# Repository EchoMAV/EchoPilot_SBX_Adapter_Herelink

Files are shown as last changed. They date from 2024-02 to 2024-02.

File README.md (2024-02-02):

Created using KiCad 7.0.10

This is an open-source radio adapter designed for the EchoPilot SBX series of boards. It is meant for a Herelink v1.1+ air unit, but can also be used for serial telemetry and IP radios such as the RFD900 or Doodle Labs.

The board provides regulated 7.5VDC @ 2A

6 Layer PCB, 4/4 mil spacing, min hole size is 0.2mm Note impedance controlled traces for MIPI, USB and Ethernet. Trace width and spacing may need to be adjusted depending on the stackup and materials used in production.

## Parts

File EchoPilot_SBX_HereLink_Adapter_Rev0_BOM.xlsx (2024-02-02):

EchoPilot SBX HereLink Radio Adapter Rev 0
Item | Qty | Reference(s) | Value | LibPart | Footprint | Part Num
1 | 1 | C1 | 4.7nF | Device:C | Capacitor_SMD:C_0201_0603Metric | GRM033R61E472KA12D
2 | 1 | C2 | 47uF | Device:C | Capacitor_SMD:C_1206_3216Metric | C3216X5R1E476M160AC
3 | 1 | C3 | 0.1uF 100V | Device:C | Capacitor_SMD:C_0603_1608Metric | CL10B104KC8NNNC
4 | 1 | C4 | 10uF 63V | Device:C | Capacitor_SMD:C_1210_3225Metric | CL32B106KMVNNWE
5 | 1 | D1 | D_Zener | Device:D_Zener | Diode_SMD:D_SMA | SK220A
6 | 1 | D2 | LED_G | Device:LED | LED_SMD:LED_0603_1608Metric | 150060VS75000
7 | 1 | IC1 | LMR14020SQDPRRQ1 | LMR14020SQDPRRQ1:LMR14020SQDPRRQ1 | SON80P400X400X80-11N | LMR14020SQDPRRQ1
8 | 1 | J1 | DF40C-30DP-0.4V(51) | Connector_Generic:Conn_02x15_Top_Bottom | UVDL.Pretty:HRS_DF40C-30DP-0.4V_51_ | DF40C-30DP-0.4V(51)
9 | 1 | J2 | Conn_01x05 | Connector_Generic:Conn_01x05 | Connector_JST:JST_GH_SM05B-GHS-TB_1x05-1MP_P1.25mm_Horizontal | SM05B-GHS-TBT
10 | 1 | J3 | Conn_01x02 | Connector_Generic:Conn_01x02 | Connector_JST:JST_GH_SM02B-GHS-TB_1x02-1MP_P1.25mm_Horizontal | SM02B-GHS-TBT
11 | 1 | J4 | Conn_01x04 | Connector_Generic:Conn_01x04 | Connector_JST:JST_GH_SM04B-GHS-TB_1x04-1MP_P1.25mm_Horizontal | SM04B-GHS-TBT
12 | 1 | J5 | Conn_01x03 | Connector_Generic:Conn_01x03 | Connector_JST:JST_GH_SM03B-GHS-TB_1x03-1MP_P1.25mm_Horizontal | SM03B-GHS-TBT
13 | 1 | L1 | 4.7uF | Device:L | UVDL.Pretty:IND_336047_WRE | 74438336047
14 | 1 | R1 | 23.2K | Device:R | Resistor_SMD:R_0201_0603Metric | ERJ-1GNF2322C
15 | 1 | R2 | 90.9K | Device:R | Resistor_SMD:R_0201_0603Metric | ERJ-1GNF9092C
16 | 1 | R3 | 10K | Device:R | Resistor_SMD:R_0201_0603Metric | ERJ-1GNF1002C
17 | 1 | R4 | 1.0K | Device:R | Resistor_SMD:R_0201_0603Metric | ERJ-1GEF1001C

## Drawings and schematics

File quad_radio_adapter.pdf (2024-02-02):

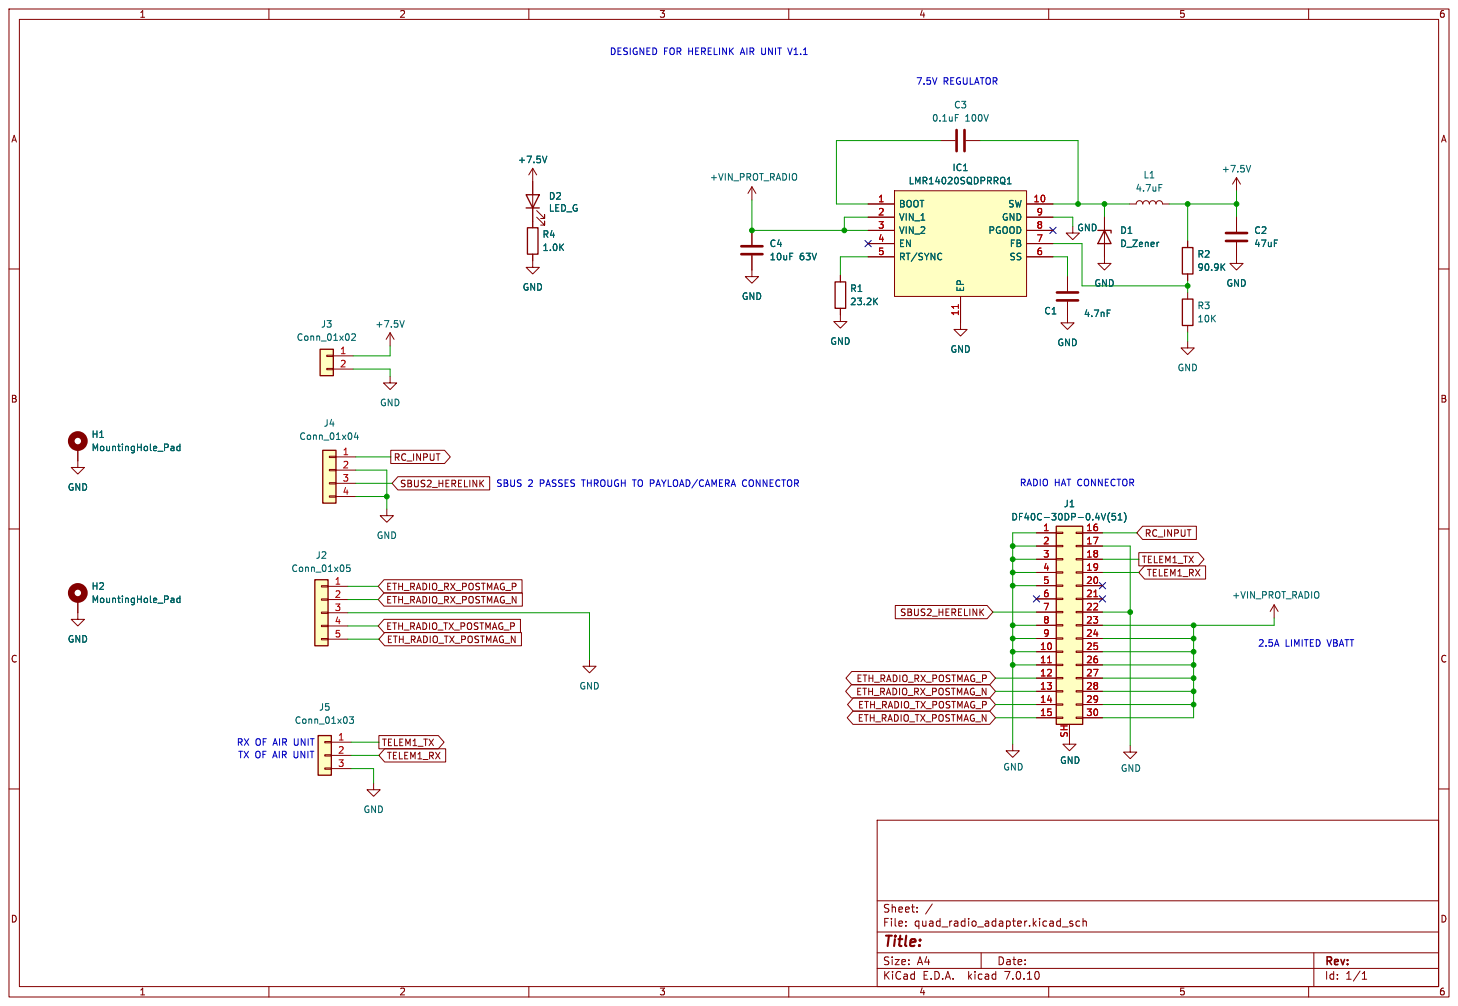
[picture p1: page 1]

TX OF AIR UNIT RX OF AIR UNIT

Id: 1/1 Title: File: quad_radio_adapter.kicad_sch Sheet: /

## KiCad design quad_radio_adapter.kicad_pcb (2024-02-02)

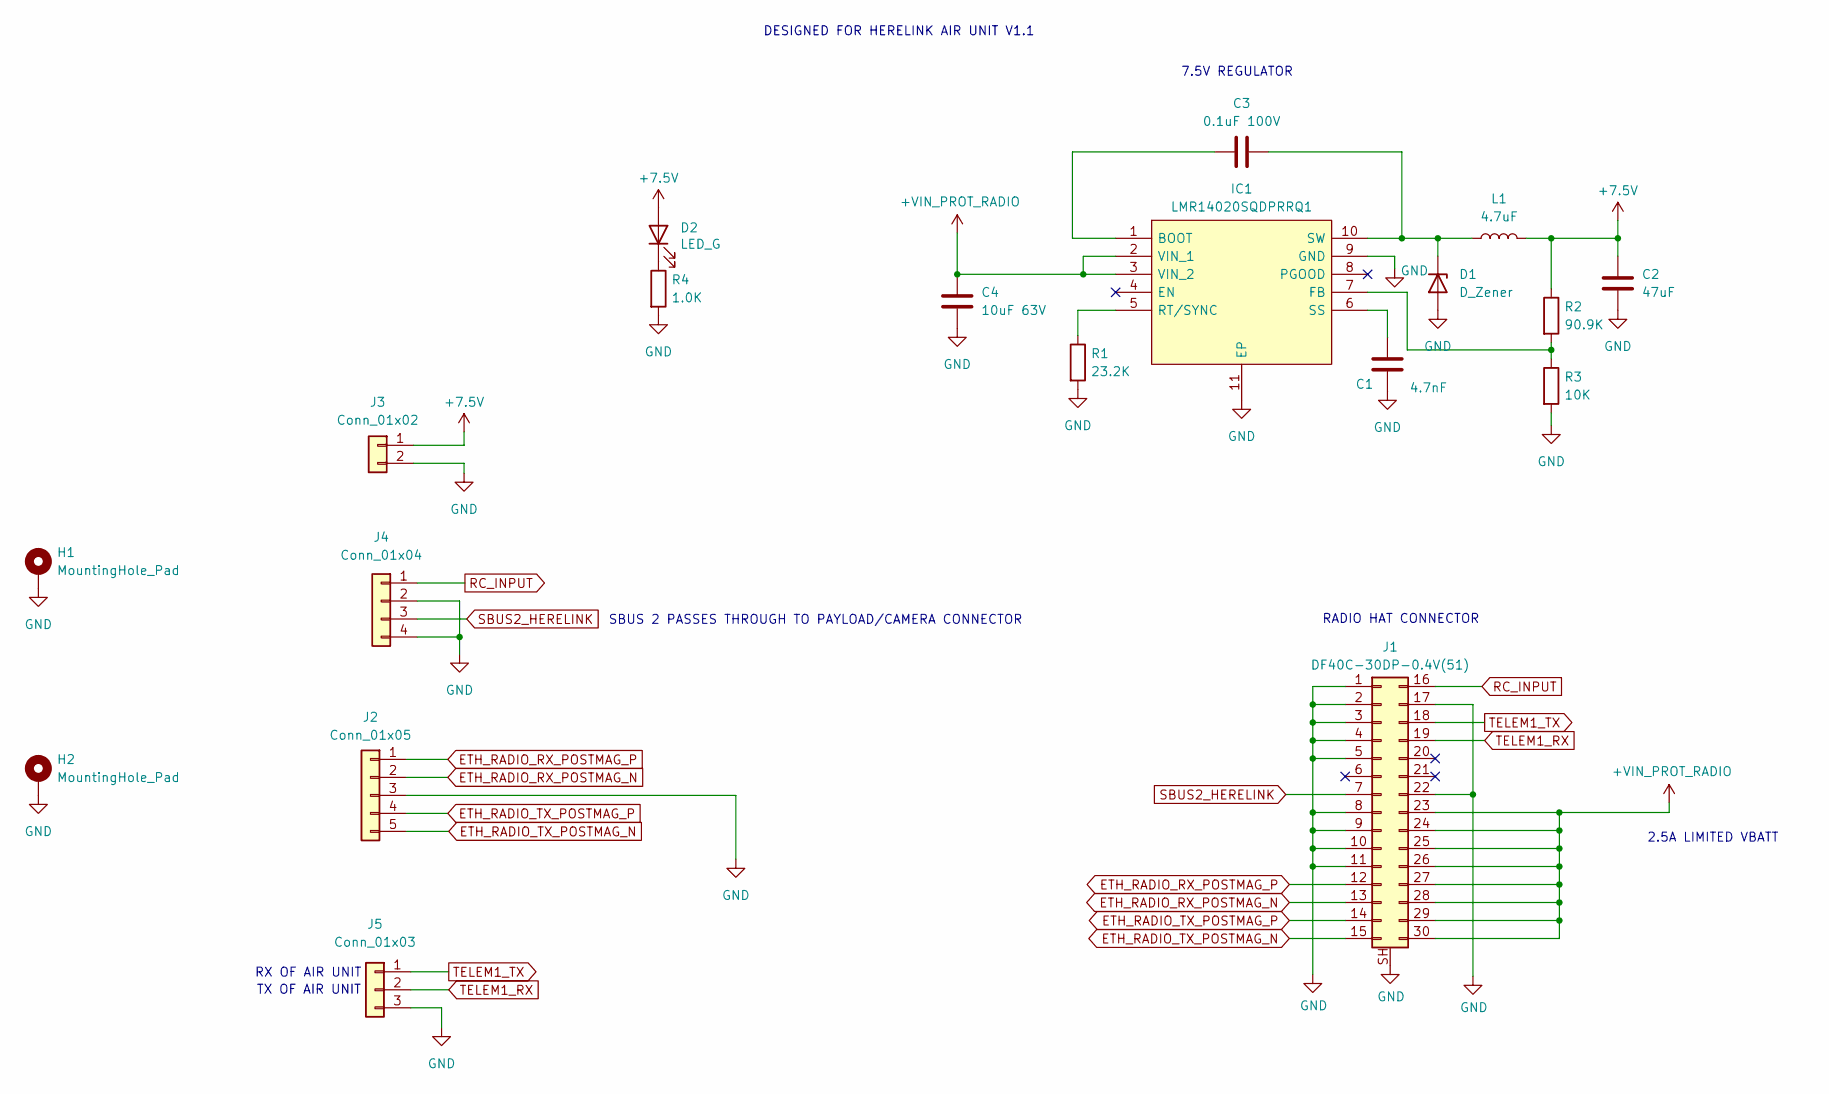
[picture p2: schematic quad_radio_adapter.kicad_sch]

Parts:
C1: 4.7nF; C_0201_0603Metric; Part Num GRM033R61E472KA12D
C2: 47uF; C_1206_3216Metric; Part Num C3216X5R1E476M160AC
C3: 0.1uF 100V; C_0603_1608Metric; Part Num CL10B104KC8NNNC
C4: 10uF 63V; C_1210_3225Metric; Part Num CL32B106KMVNNWE
D1: D_Zener; D_SMA; Part Num SK220A
D2: LED_G; LED_0603_1608Metric; Part Num 150060VS75000
H1, H2: MountingHole_Pad; MountingHole_2.2mm_M2_Pad
IC1: LMR14020SQDPRRQ1; SON80P400X400X80-11N; Manufacturer_Part_Number LMR14020SQDPRRQ1; Mouser Part Number 595-LMR14020SQDPRRQ1
J1: DF40C-30DP-0.4V(51); HRS_DF40C-30DP-0.4V_51_; Part Num DF40C-30DP-0.4V(51)
J2: Conn_01x05; JST_GH_SM05B-GHS-TB_1x05-1MP_P1.25mm_Horizontal; Part Num SM05B-GHS-TBT
J3: Conn_01x02; JST_GH_SM02B-GHS-TB_1x02-1MP_P1.25mm_Horizontal; Part Num SM02B-GHS-TBT
J4: Conn_01x04; JST_GH_SM04B-GHS-TB_1x04-1MP_P1.25mm_Horizontal; Part Num SM04B-GHS-TBT
J5: Conn_01x03; JST_GH_SM03B-GHS-TB_1x03-1MP_P1.25mm_Horizontal; Part Num SM03B-GHS-TBT
L1: 4.7uF; IND_336047_WRE; Part Num 74438336047
R1: 23.2K; R_0201_0603Metric; Part Num ERJ-1GNF2322C
R2: 90.9K; R_0201_0603Metric; Part Num ERJ-1GNF9092C
R3: 10K; R_0201_0603Metric; Part Num ERJ-1GNF1002C
R4: 1.0K; R_0201_0603Metric; Part Num ERJ-1GEF1001C

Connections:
+7.5V: C2.1, D2.2 (A), J3.1, L1.2, R2.1
+VIN_PROT_RADIO: C4.1, IC1.2 (VIN_1), IC1.3 (VIN_2), J1.23, J1.24, J1.25, J1.26, J1.27, J1.28, J1.29, J1.30
ETH_RADIO_RX_POSTMAG_N: J1.13, J2.2
ETH_RADIO_RX_POSTMAG_P: J1.12, J2.1
ETH_RADIO_TX_POSTMAG_N: J1.15, J2.5
ETH_RADIO_TX_POSTMAG_P: J1.14, J2.4
GND: C1.2, C2.2, C4.2, D1.2 (A), H1.1, H2.1, IC1.9 (GND), IC1.11 (EP), J1.1, J1.2, J1.3, J1.4, J1.5, J1.8, J1.9, J1.10, J1.11, J1.17, J1.22, J1.SH, J2.3, J3.2, J4.2, J4.4, J5.3, R1.2, R3.2, R4.2
unnamed: C3.2, D1.1 (K), IC1.10 (SW), L1.1
unnamed: D2.1 (K), R4.1
unnamed: C3.1, IC1.1 (BOOT)
unnamed: IC1.7 (FB), R2.2, R3.1
unnamed: IC1.5 (RT/SYNC), R1.1
unnamed: C1.1, IC1.6 (SS)
RC_INPUT: J1.16, J4.1
SBUS2_HERELINK: J1.7, J4.3
TELEM1_RX: J1.19, J5.2
TELEM1_TX: J1.18, J5.1

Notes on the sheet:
RX OF AIR UNIT
7.5V REGULATOR
2.5A LIMITED VBATT
RADIO HAT CONNECTOR
TX OF AIR UNIT
SBUS 2 PASSES THROUGH TO PAYLOAD/CAMERA CONNECTOR
DESIGNED FOR HERELINK AIR UNIT V1.1

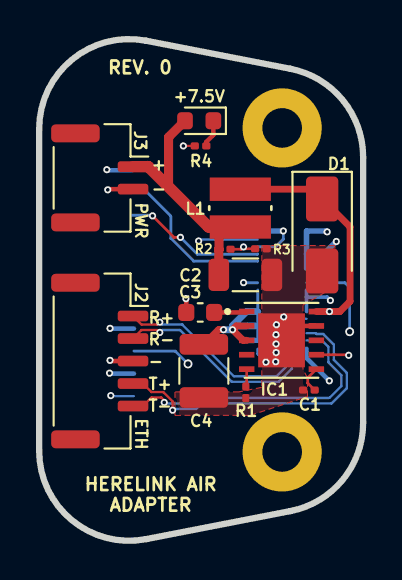
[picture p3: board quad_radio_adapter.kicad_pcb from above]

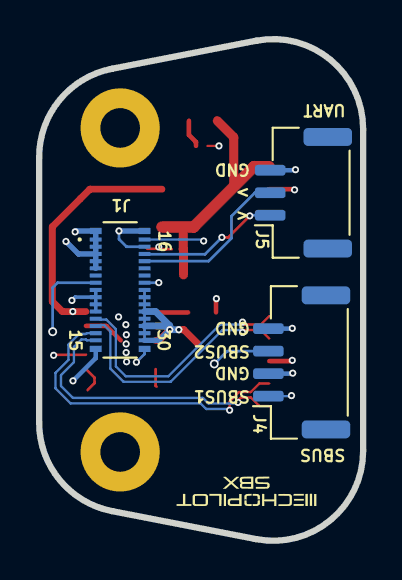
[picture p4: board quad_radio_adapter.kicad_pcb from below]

Board: 6 copper layers, 18.0 x 27.9 mm, 19 parts (3 on the bottom side), 17 nets.
